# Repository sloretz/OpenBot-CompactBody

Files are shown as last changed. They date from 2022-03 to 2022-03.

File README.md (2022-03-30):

# OpenBot - Compact Body

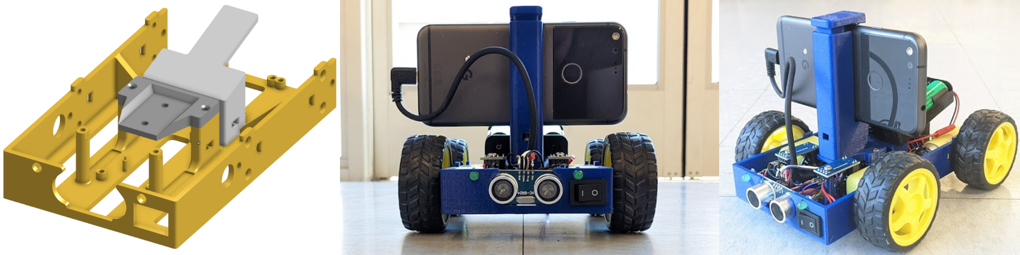
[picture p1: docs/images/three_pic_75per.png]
Left: OpenBot-CompactBody in CAD; Center: Front view of assembled robot; Right: Angled view of assembled robot


This is an alternative to the original [OpenBot](https://www.openbot.org/) body that can be made faster, with less plastic, and on 3d printers with smaller build volumes.
The minimum build volume is **161 x 100 x 32mm**.

Most components (motors, wheels, phone, sonar, encoders) are in the exact same positions as the original.
This means the kinematics are the same, and a [URDF](http://wiki.ros.org/urdf) or [SDFormat](http://sdformat.org/) file for the original may still be usable with the Compact Body.
There are few exceptions:
  * The LEDs are mounted on the front instead of the rear
  * There is no space for the optional OLED screen
  * The power switch is mounted on the front instead of the top

## Printing it

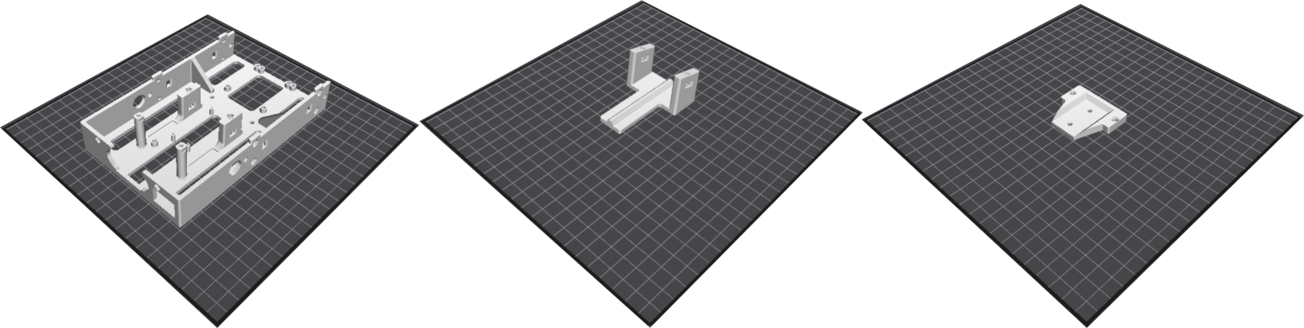
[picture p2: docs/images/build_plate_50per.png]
All parts and their orientation on a build plate


Parts:
  
* `compact_body` [.stl](cad/compact_body.stl) [.step](cad/compact_body.step)
* `compact_phone_plate` [.stl](cad/compact_phone_plate.stl) [.step](cad/compact_phone_plate.step)
* `compact_battery_mount` [.stl](cad/compact_battery_mount.stl) [.step](cad/compact_battery_mount.step)

You'll also need to print the original [`phone_mount_bottom` and `phone_mount_top`](https://github.com/isl-org/OpenBot/tree/e99d19224f31dc0bd887e847b58db6c55c3338ed/body/diy#3d-printing).

See the photo above for orientation on the build plate.
A layer height of 0.2mm is sufficient, and no supports are needed.
Infill around 15-20% is fine.
It's been tested with PETG, but any other rigid plastic should work too.

## Assembly

### 1. Hot glue M3 nuts before making electrical connections

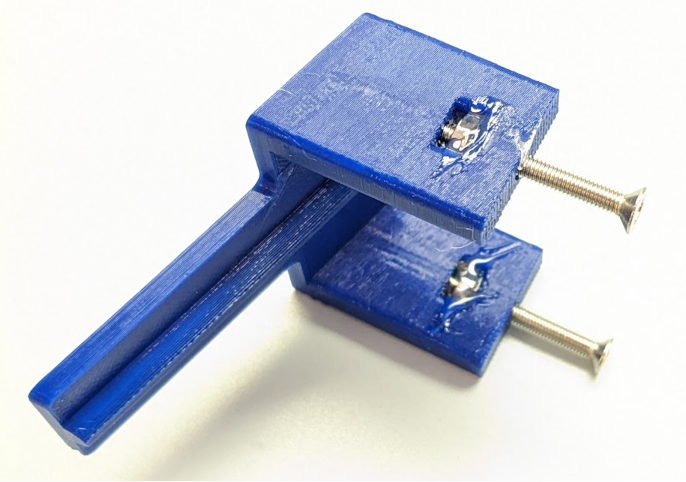
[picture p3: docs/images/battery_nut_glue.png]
Battery mount with nuts being glued


Hot glue the nuts for the battery mount and phone plate before beginning the rest of the assembly.
Insert the nuts into the slots and thread the screws through them.
Pull on the screw to seat the nut, then hot glue it.
Remove the screws when the glue solidifies.

### 2. Mount components and solder all electrical connections

Follow the [OpenBot DIY assembly instructions](https://github.com/isl-org/OpenBot/tree/e99d19224f31dc0bd887e847b58db6c55c3338ed/body/diy#assembly).

The compact body was tested with the DIY wiring option.
Here's what it looks like with all wires connected.

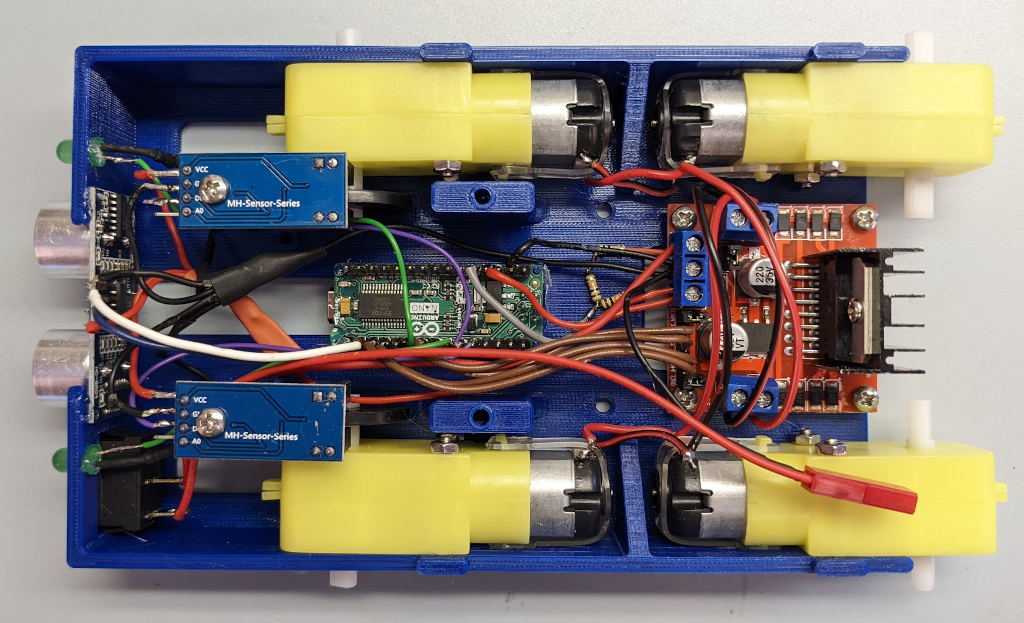
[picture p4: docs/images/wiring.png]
Wiring inside of the robot


The compact body has points for a PCB to be mounted using four (4) M3x5 screws.
The four (4) Arduino Nano stands need to be broken off to use them.

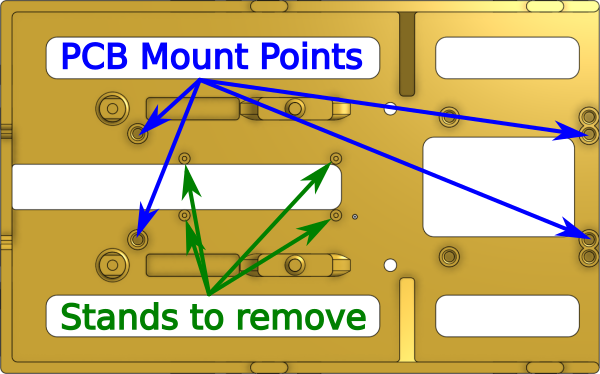
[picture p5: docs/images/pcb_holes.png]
Picture of PCB mount points


**Only break off the stands if you are using the OpenBot PCB. Do not break them off otherwise.**

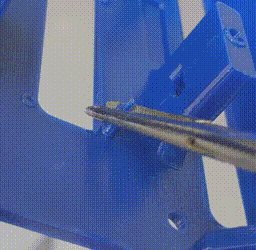
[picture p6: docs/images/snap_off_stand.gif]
Video of stand being snapped off


No testing has been done with a real PCB.
If you try it out, please open an issue to say if it works.

### 3. Mount the phone holder to the phone plate

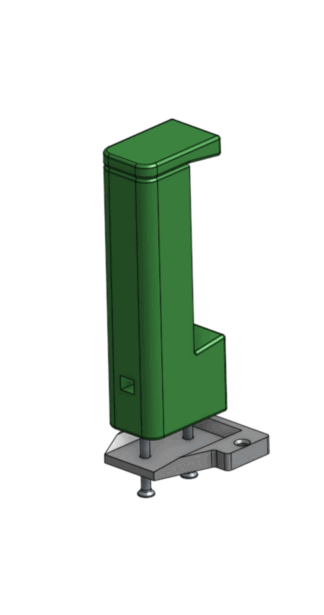
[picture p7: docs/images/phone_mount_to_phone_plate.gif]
Animation of screws connecting phone mount to phone plate


Mount the phone holder to the top of the phone plate using two (2) M3x25 screws and M3 nuts.

### 4. Attach the phone plate to the body

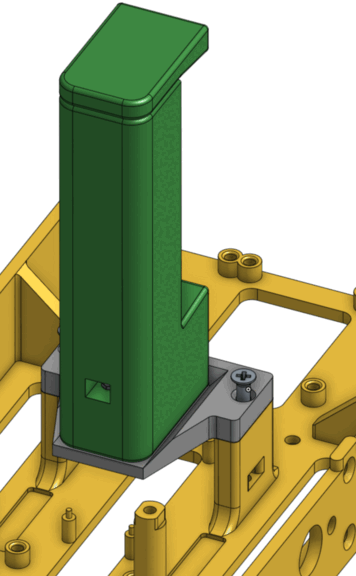
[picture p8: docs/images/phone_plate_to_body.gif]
Animation of screws connecting phone plate to compact body


Attach the phone plate using two (2) M3x25 screws and M3 nuts.

### 5. Attach the battery mount to the body

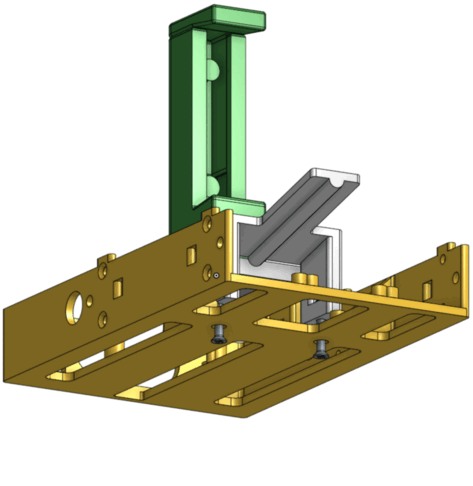
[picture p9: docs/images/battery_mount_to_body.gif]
Animation of screws connecting battery mount to compact body


Attach the battery mount using two (2) M3x25 screws and M3 nuts.

### 6. Glue the battery holder to the battery mount

Put a line of hot glue onto the battery mount and press the battery holder onto it.

### Assembly complete!

Your robot should look something like this.

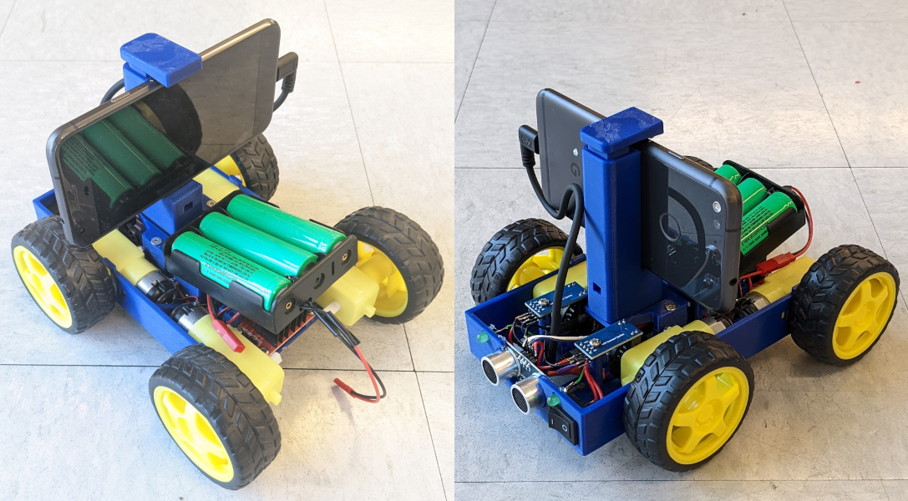
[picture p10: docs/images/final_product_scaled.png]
Two views of a full assembed robot


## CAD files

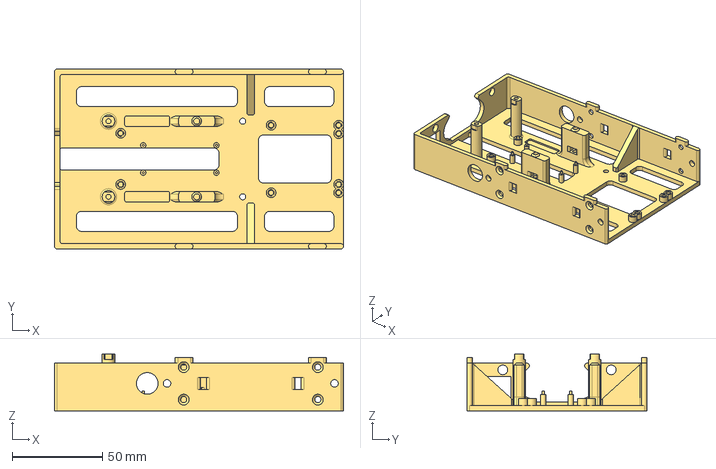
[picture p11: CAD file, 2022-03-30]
cad/compact_body.step
160.5 x 100.0 x 31.5 mm

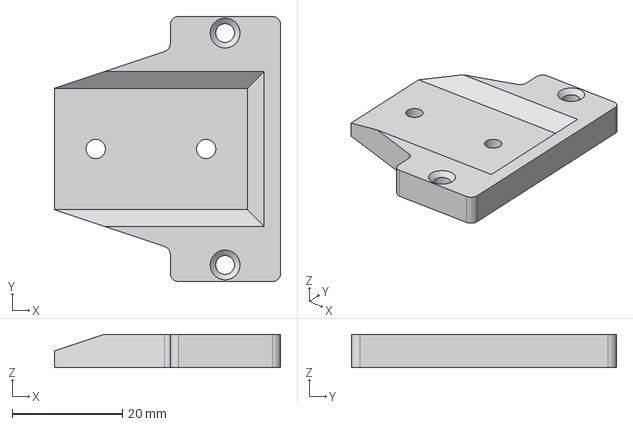
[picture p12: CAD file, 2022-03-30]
cad/compact_phone_plate.step
41.0 x 48.0 x 6.00 mm

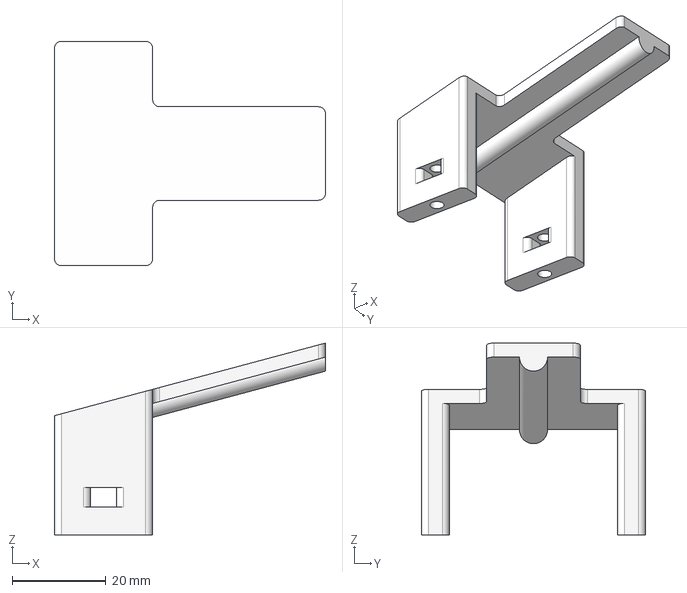
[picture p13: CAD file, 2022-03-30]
cad/compact_battery_mount.step
58.0 x 48.0 x 41.0 mm

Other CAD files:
cad/compact_battery_mount.stl
cad/compact_phone_plate.stl
